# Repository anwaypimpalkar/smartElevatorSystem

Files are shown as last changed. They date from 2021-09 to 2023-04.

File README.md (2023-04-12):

# Smart Elevator Systems using Embedded Machine Learning and Fire Safety Mechanisms

April - June 2021 | Micro Project in SY BTech

### Updates
- ***June 2021:** Awarded "Best Project" out of a pool of 1000+ projects at the 5th IEEE National Level Project Competition.*

- ***January 2022:** Check out the [Arduino Team's Blog Post](https://blog.arduino.cc/2022/01/29/this-contactless-system-combines-embedded-ml-and-sensors-to-improve-elevator-safety/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) covering this project!*

## Introduction

Using an approach of Embedded Machine Learning, we built a multi-tenant architecture to facilitate a contactless elevator system. It consists of two parts – person detection and speech recognition. To create an effective pipeline, we used multiple signal processing techniques to extract necessary features from the input signals. Further, we developed a fire safety system using basic yet functional sensors in two methods – using a microcontroller and using an operational amplifier. These systems are deployed outside and inside an elevator, respectively. Lastly, we built a PCB to house all these components and make a holistically deployable product.

## High-Level Process Flow

First, we would want a person to come and stand in front of the elevator, indicating that he wants to use it. 
Then, the person would speak the floor number he would like to visit, and the elevator system recognizes the floor number which was spoken. The elevator then operates as it should and the doors should open for him. The overall flow of the system is shown in the figure below.

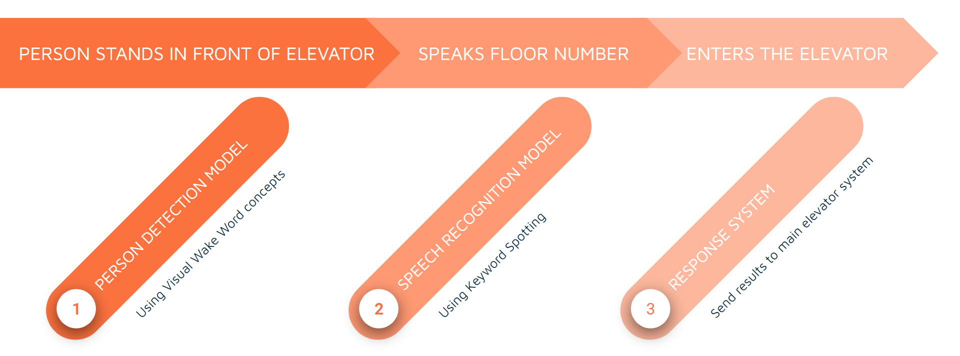
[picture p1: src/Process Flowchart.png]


## System Overview

The project is a three-part system encompassing the following subsystems:

1. Person recognition (VWW Detection) and voice recognition (KWS) to operate the elevator.

2. Fire safety mechanism inside the elevator to drop installed oxygen masks and signal the main elevator interface.

3. Fire safety and detection system outside the elevator on different floors bundled with the features mentioned in point (1).

A generic block diagram of the entire system is shown below.

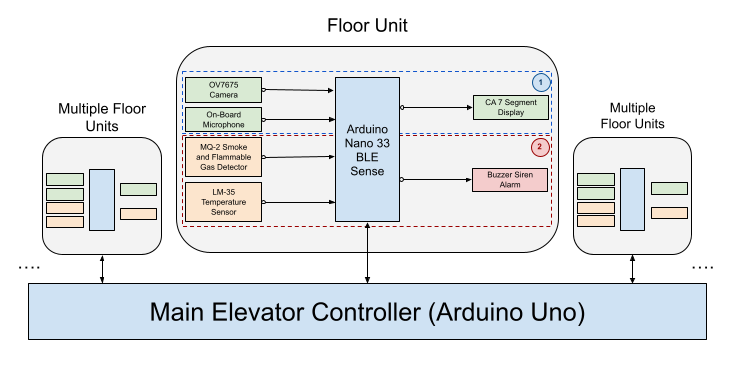
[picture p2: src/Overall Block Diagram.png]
   

## Contactless Operation using KWS and VWW CNN Models

The KWS and VWW models are combined in a multi-tenant architecture. In such a structure, only one of the two models runs inference on the input data at a time. This allows for fast inferences and efficient memory allocation when and wherever required. As our development board of choice - *Arduino Nano 33 BLE Sense*, has limited resources available on board (1MB CPU Flash Memory, 256KB SRAM), the neural network on the system had to be memory and energy efficient compared to a whole scale neural network model. Further post-training quantization methods were implemented to reduce the size of the model (KWS model: 26,720 bytes; VWW model: 3,00,568 bytes; Total size after compilation: 207712 bytes 79% of dynamic memory) and latency of the inferences in real time.

#### Visual Wake Word (VWW) Model for Person Detection

The Visual Wake Word model used for our elevator use case is based on an existing MobileNets model. The core concept behind the architecture is depthwise separable convolution. This is a variant of classical two-dimensional convolutions that works in a much more efficient way, without compromising on accuracy greatly. The model has various steps, as shown in the figure below. Namely, these steps are Initialization, Pre-Processing, Model Inference, and Response.

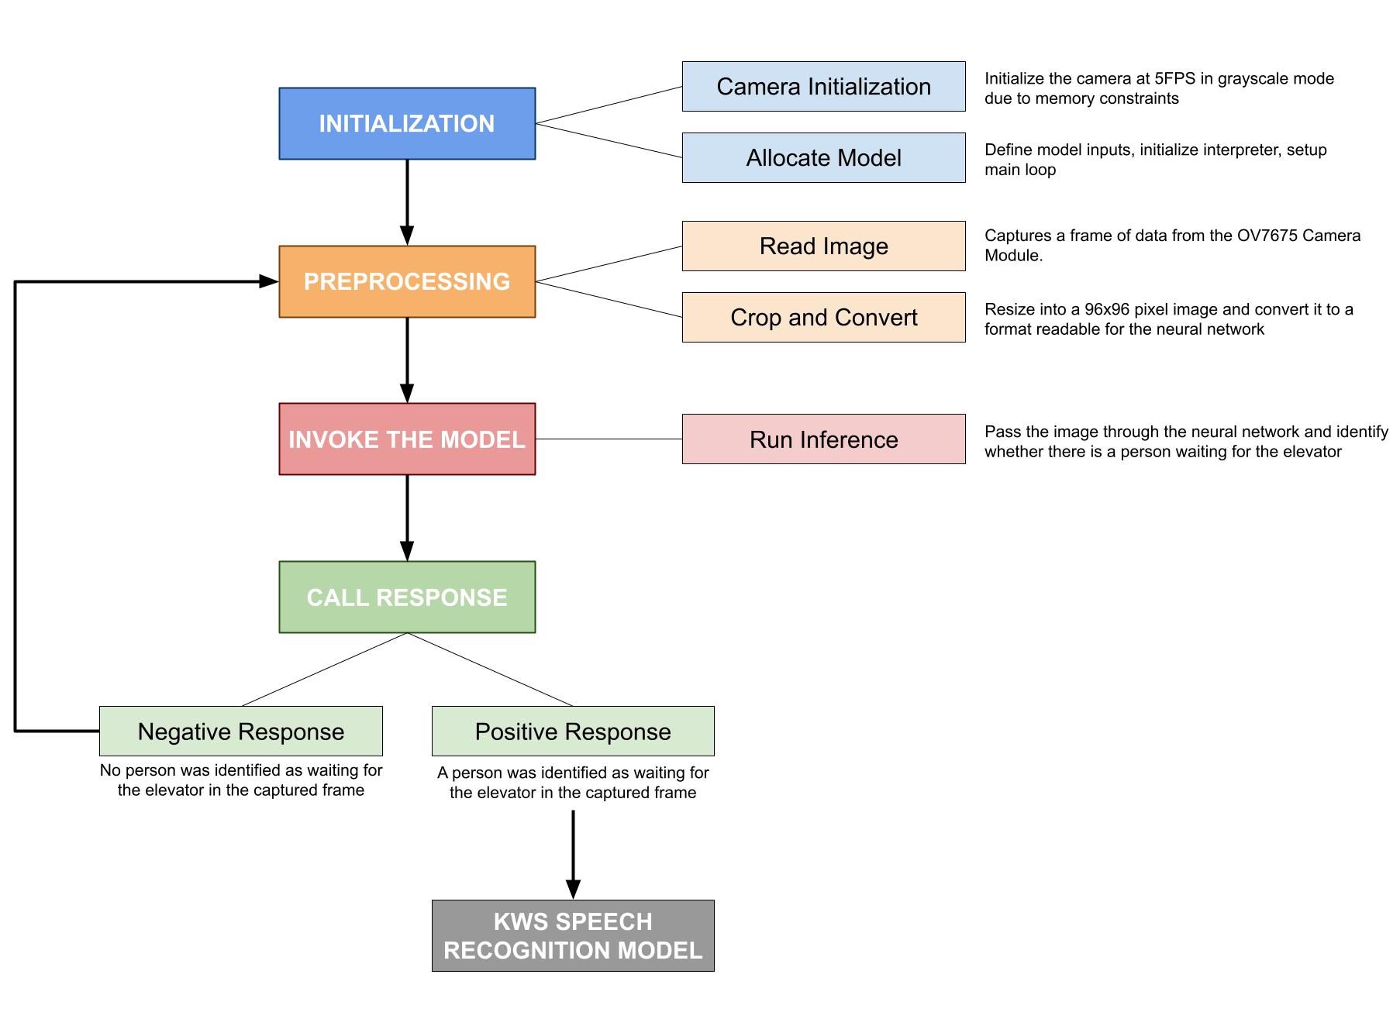
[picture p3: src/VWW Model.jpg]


#### Keyword Spotting (KWS) Model for Speech Recognition

To enable a completely contactless experience for the elevator interface, we implemented a speech recognition approach to choose the floor number that a given user would like to go to. We went on to implement a KWS (Keyword Spotting) model to satisfy this requirement. The chosen keywords were floor numbers in the lower order “One”, “Two”, “Three” and “Four”. Like the VWW model, the KWS model has 4 high level steps in the system as shown in the figure below. Compared to the prior, this model is relatively lightweight and takes lesser time for training and inference.

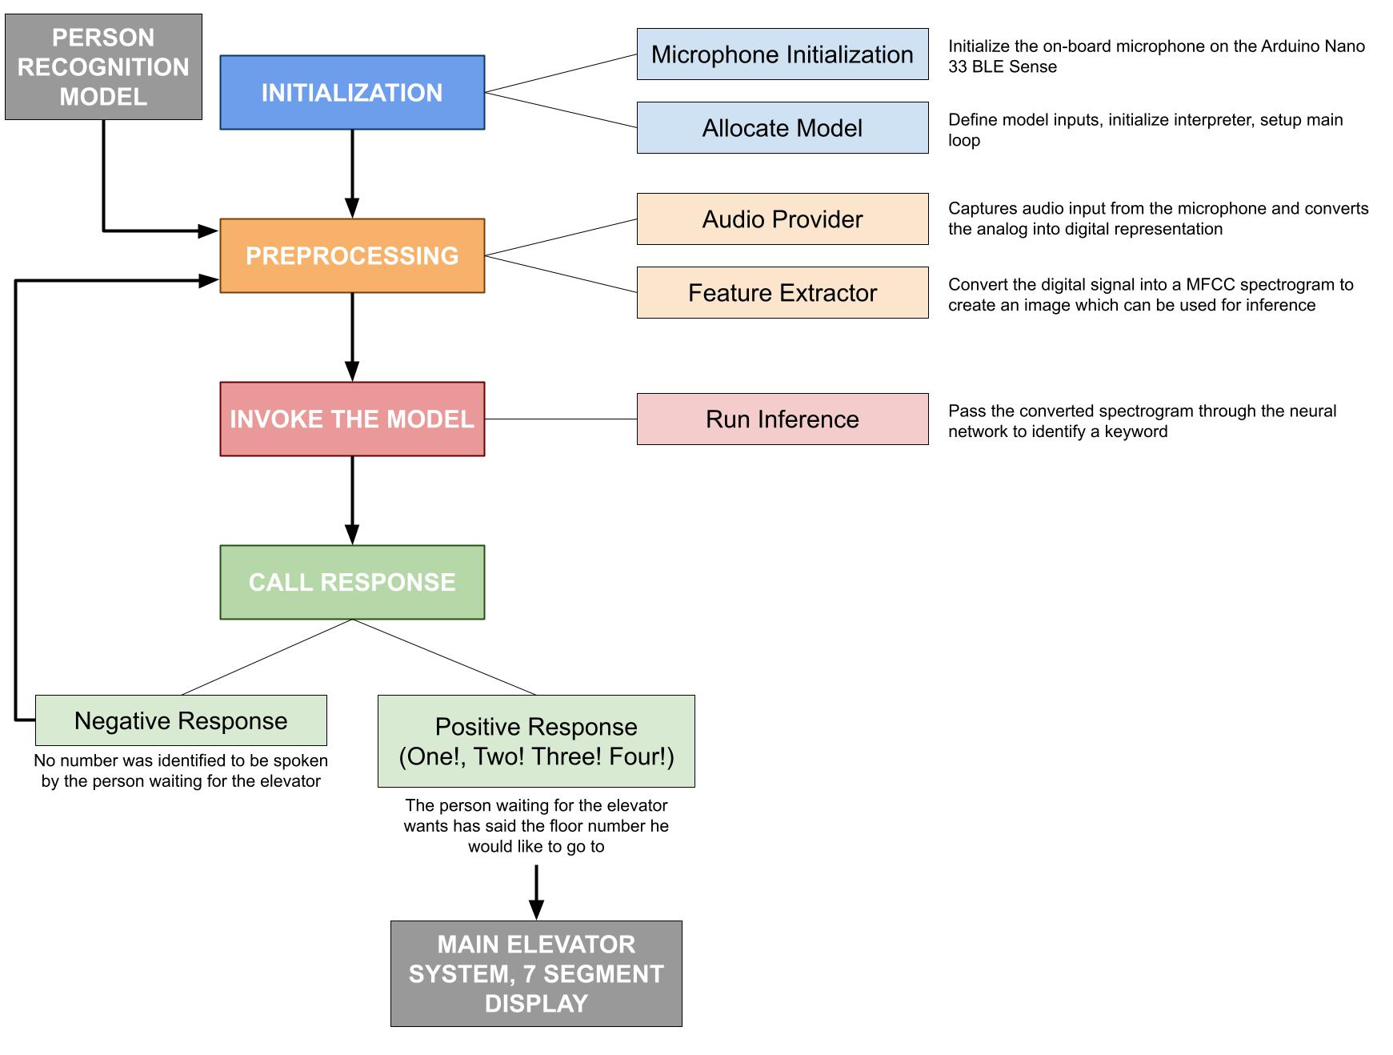
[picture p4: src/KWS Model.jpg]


To make it easier for the CNN to process and classify the audio signals into different categories, we extract the features of the buffer audio sample before passing it into an inference pipeline. The various steps of feature extraction are:

- Fast Fourier Transform (FFT)
- Frequency Domain Spectrograms
- Mel Frequency Cepstral Coefficient Spectrograms

#### Multitenant Architecture for Running KWS and VWW Simultaneously

Due to the memory and power constraints on any embedded microcontroller, running two CNN inference engines simultaneously is a challenge. Our approach to this problem was to implement a multi-tenant architecture for combining the KWS and VWW model. In such a structure, only one of the two models runs inference on the input data at a time. Both models share the TensorArena and use the same memory allocations. This allowed for fast inferences and efficient memory allocation when and wherever required. There is also no requirement for the synchronization of data streams from the camera module and the microphone, both of which are running at different sampling rates.

## Fire Safety System

Elevator shafts may be exposed to smoke and that smoke could reach occupants not just inside the elevator but on other floors as well. In such situations, the elevator is advised to return to the ground floor of the building immediately. The most efficient way to develop a fire safety system which protects the occupants of an elevator is to design a system which works in tandem with it the smoke/flammable gas detectors and temperature sensors directly. To maximize the efficiency of such a system, we developed a pipeline in which the main elevator interface has direct inputs from the smoke detection units. Depending on the levels obtained from the sensors, the elevator interface can further be commanded to execute a specific set of instructions, for example taking the elevator to the lowest floor immediately in the case of a fire.

To implement our approach, we chose to use a MQ-2 Smoke/Flammable Gas Detector and a LM-35 Temperature sensor.

## Implementation and Results

The hardware required for the implementation of the contactless elevator system, i.e., the VWW and KWS models was readily available with us, namely the Arduino Nano 33 BLE Sense and OV7675 Camera Module. They are mounted on a shield for the scope of this experiment. Further into the implementation, we designed our own shield to house the OV7675 and Arduino module along with other peripherals.

Once the shield was properly positioned, we ran inference by standing inside and outside the frame of the camera. As discussed in the System Architecture chapter, each inference returns a probability value between -127 and +127, where higher numbers indicate a higher probability of a human subject being present in the frame.

The camera input of greyscale QCIF images of size 144 x 176 pixels with human subject are shown below.

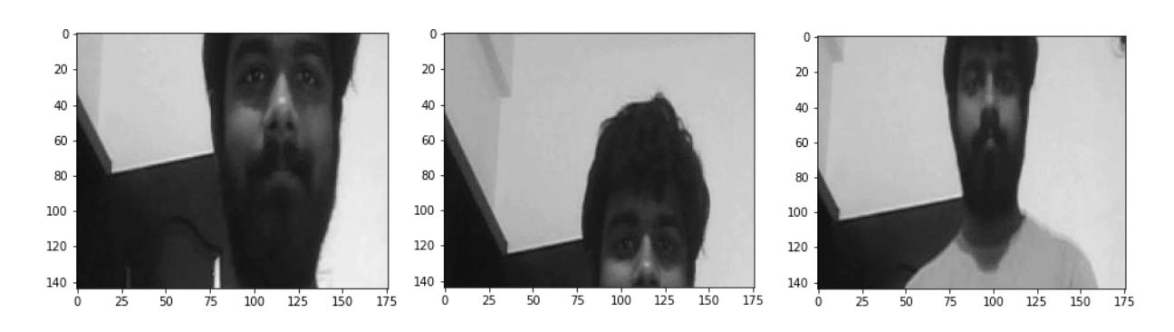
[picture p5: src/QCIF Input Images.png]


Once the inference engine is run, the probability values are generated. These values are printed on the serial monitor of the Arduino IDE. When a person is entering the frame or in motion, the camera is unable to pick up the fast movement due to the low frame rate. At such moments, the model is decisive of whether a person is the frame or not. Hence, while classifying as a human detected in the field of view, we chose to keep a minimum Person score of 25. This threshold value reduces the number of false positives. If a person is detected in the frame, the green RGB light on the Arduino is lit up, whereas when there is no person detected, the red RGB light is lit up.

Once a person has been detected in the frame, the KWS model inference engine is triggered, and the system starts listening for keywords spoken by the user to communicate the floor number which they would like to go to. These numbers are chosen to be “One”, “Two”, “Three”, and “Four”. The incoming audio is sampled at 16 kHz and ran inference on every one second. Whenever the Arduino is listening for a keyword, the yellow light rapidly blinks, and upon positive inference, the blue RGB light is lit up. The different LED states are shown in the image below.

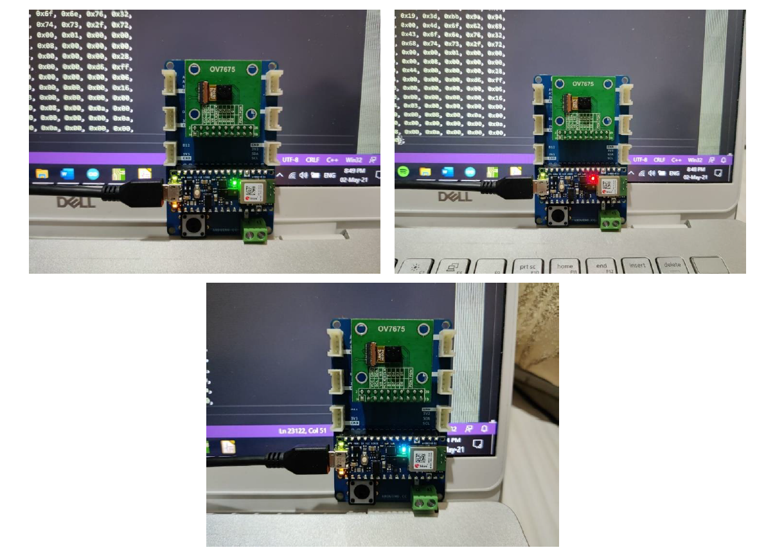
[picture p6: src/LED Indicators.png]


The fire safety system outside the elevator bundled with the deployed unit was simulated on Proteus. The system consisted of the following components:
1. MQ-2 Smoke Detector System
2. LM-35 Temperature Sensor
3. 7 Segment Display using Shift Register
4. Alarm and Connection to Main Elevator Interface

Since the Arduino Nano 33 BLE Sense was not available as a library for simulation, we used the Arduino Nano baseline model for it. The architecture is similar and hence is adequate for the purposes of the project. For the sake of completeness in the project, we chose to go create a pseudo-main elevator interface using an Arduino Uno in the simulation. A 4 x 16 LCD Display was also added for us to keep track of the system status. The figure below shows the circuit schematic for the project on Proteus. The Arduino Nano is interfaced with a LM-35 and MQ-2 sensor, a 7 Segment Display and an alarm system which is triggered when the system is simulating a fire scenario.

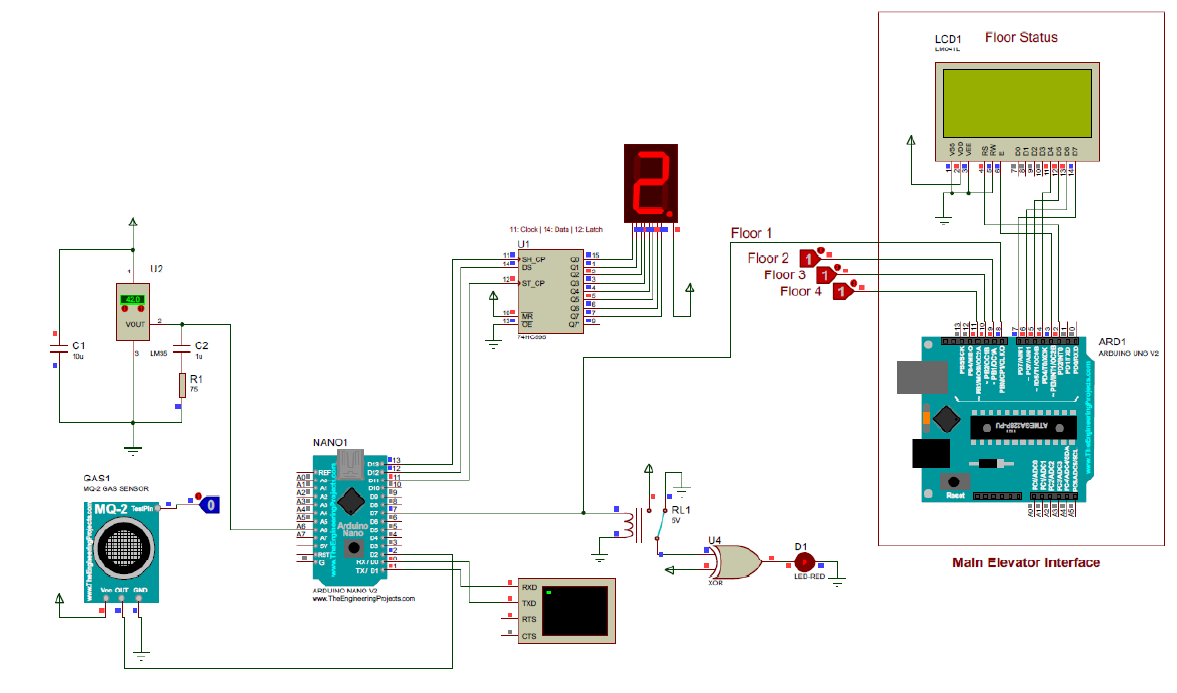
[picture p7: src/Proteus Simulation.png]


#### PCB Design

To house the components of this project, we created a Printed Circuit Board design using KiCAD, an open-source EDA software. Some key specifications of the PCB are:

1. The PCB consists of 4 Copper layers.

2. Front and Back Copper Layers are signal layers.
3. Inner1 Copper layer contains a Power Plane.
4. Inner2 Copper layer contains a Ground Plane.
5. All components used utilize Through Hole Technology (THT) except for 74AHC1G86 Dual Input Single Output EX-OR Gate which uses SMT.

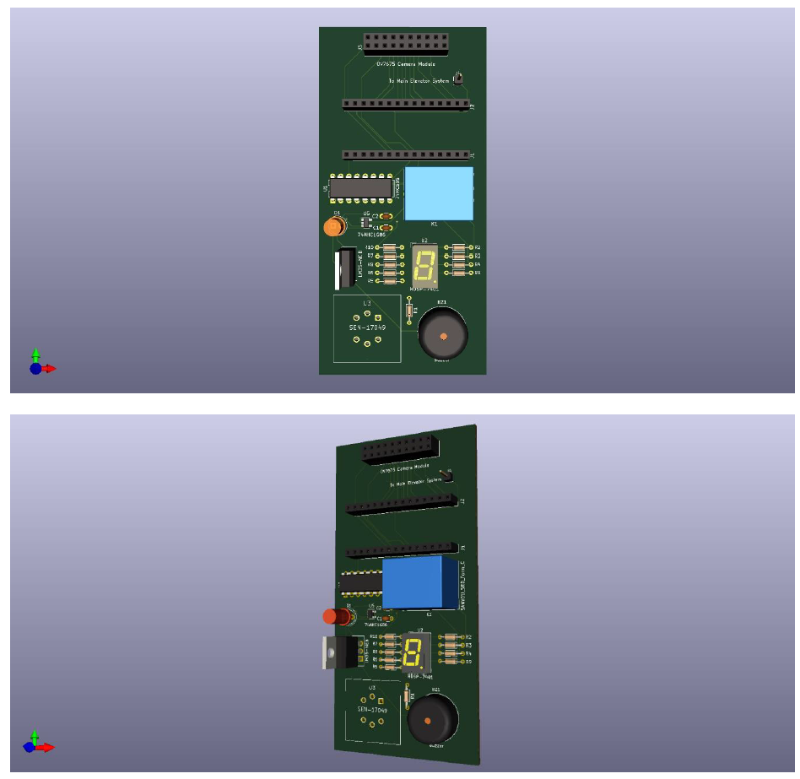
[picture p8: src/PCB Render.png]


## Demonstration

The hardware required was implemented as a proof of concept for the evaluation of the project. An unnarrated [video demonstration](https://youtu.be/mMH1OMFZL_I) has been documented.

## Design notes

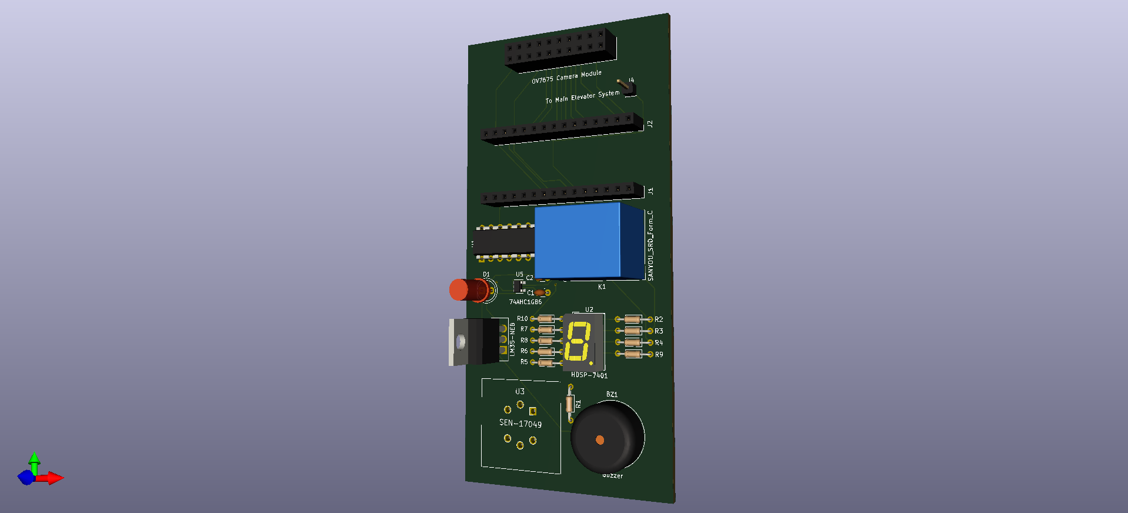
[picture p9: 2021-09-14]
KiCAD PCB Design/PCB Layout/PCB Render - 1.png

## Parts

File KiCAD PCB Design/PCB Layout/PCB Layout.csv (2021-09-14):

Id | Designator | Package | Quantity | Designation | Supplier and ref
1 | K1 | Relay_SPDT_SANYOU_SRD_Series_Form_C | 1 | SANYOU_SRD_Form_C
2 | U3 | SEN17049 | 1 | SEN-17049
3 | U4 | TO-220-3_Vertical | 1 | LM35-NEB
4 | U1 | DIP-16_W7.62mm | 1 | 74HC595
5 | J3 | PinSocket_2x10_P2.54mm_Vertical | 1 | OV7675 Camera Module
6 | J1 | PinSocket_1x15_P2.54mm_Vertical | 1 | L Arduino Mount
7 | J2 | PinSocket_1x15_P2.54mm_Vertical | 1 | R Arduino Mount
8 | U2 | HDSP-7401 | 1 | HDSP-7401
9 | BZ1 | Buzzer_15x7.5RM7.6 | 1 | Buzzer
10 | U5 | SOT-23-5 | 1 | 74AHC1G86
11 | J4 | PinHeader_1x01_P2.54mm_Vertical | 1 | To Main Elevator System
12 | R1 | R_Axial_DIN0204_L3.6mm_D1.6mm_P7.62mm_Horizontal | 1 | 4kΩ
13 | R2,R3,R4,R5,R6,R7,R8,R9 | R_Axial_DIN0204_L3.6mm_D1.6mm_P7.62mm_Horizontal | 8 | 330Ω
14 | C1 | C_Disc_D3.0mm_W1.6mm_P2.50mm | 1 | 10uF
15 | C2 | C_Disc_D3.0mm_W1.6mm_P2.50mm | 1 | 1uF
16 | R10 | R_Axial_DIN0204_L3.6mm_D1.6mm_P7.62mm_Horizontal | 1 | 75Ω
17 | D1 | LED_D5.0mm_FlatTop | 1 | LED

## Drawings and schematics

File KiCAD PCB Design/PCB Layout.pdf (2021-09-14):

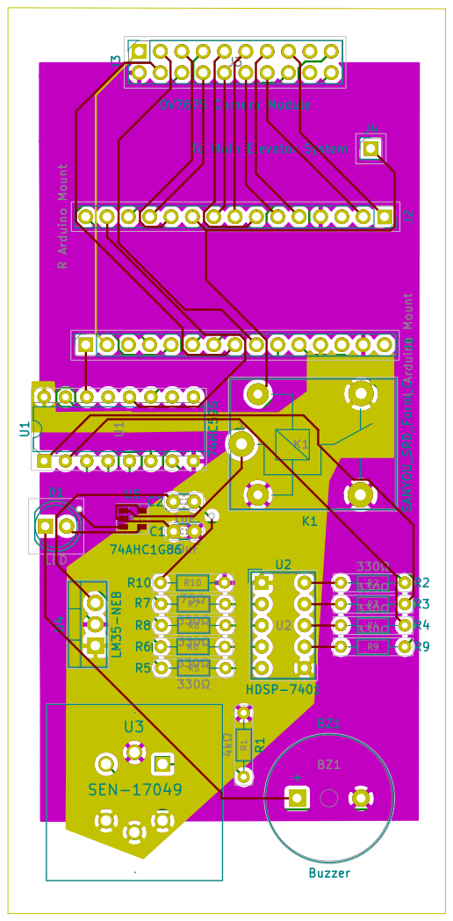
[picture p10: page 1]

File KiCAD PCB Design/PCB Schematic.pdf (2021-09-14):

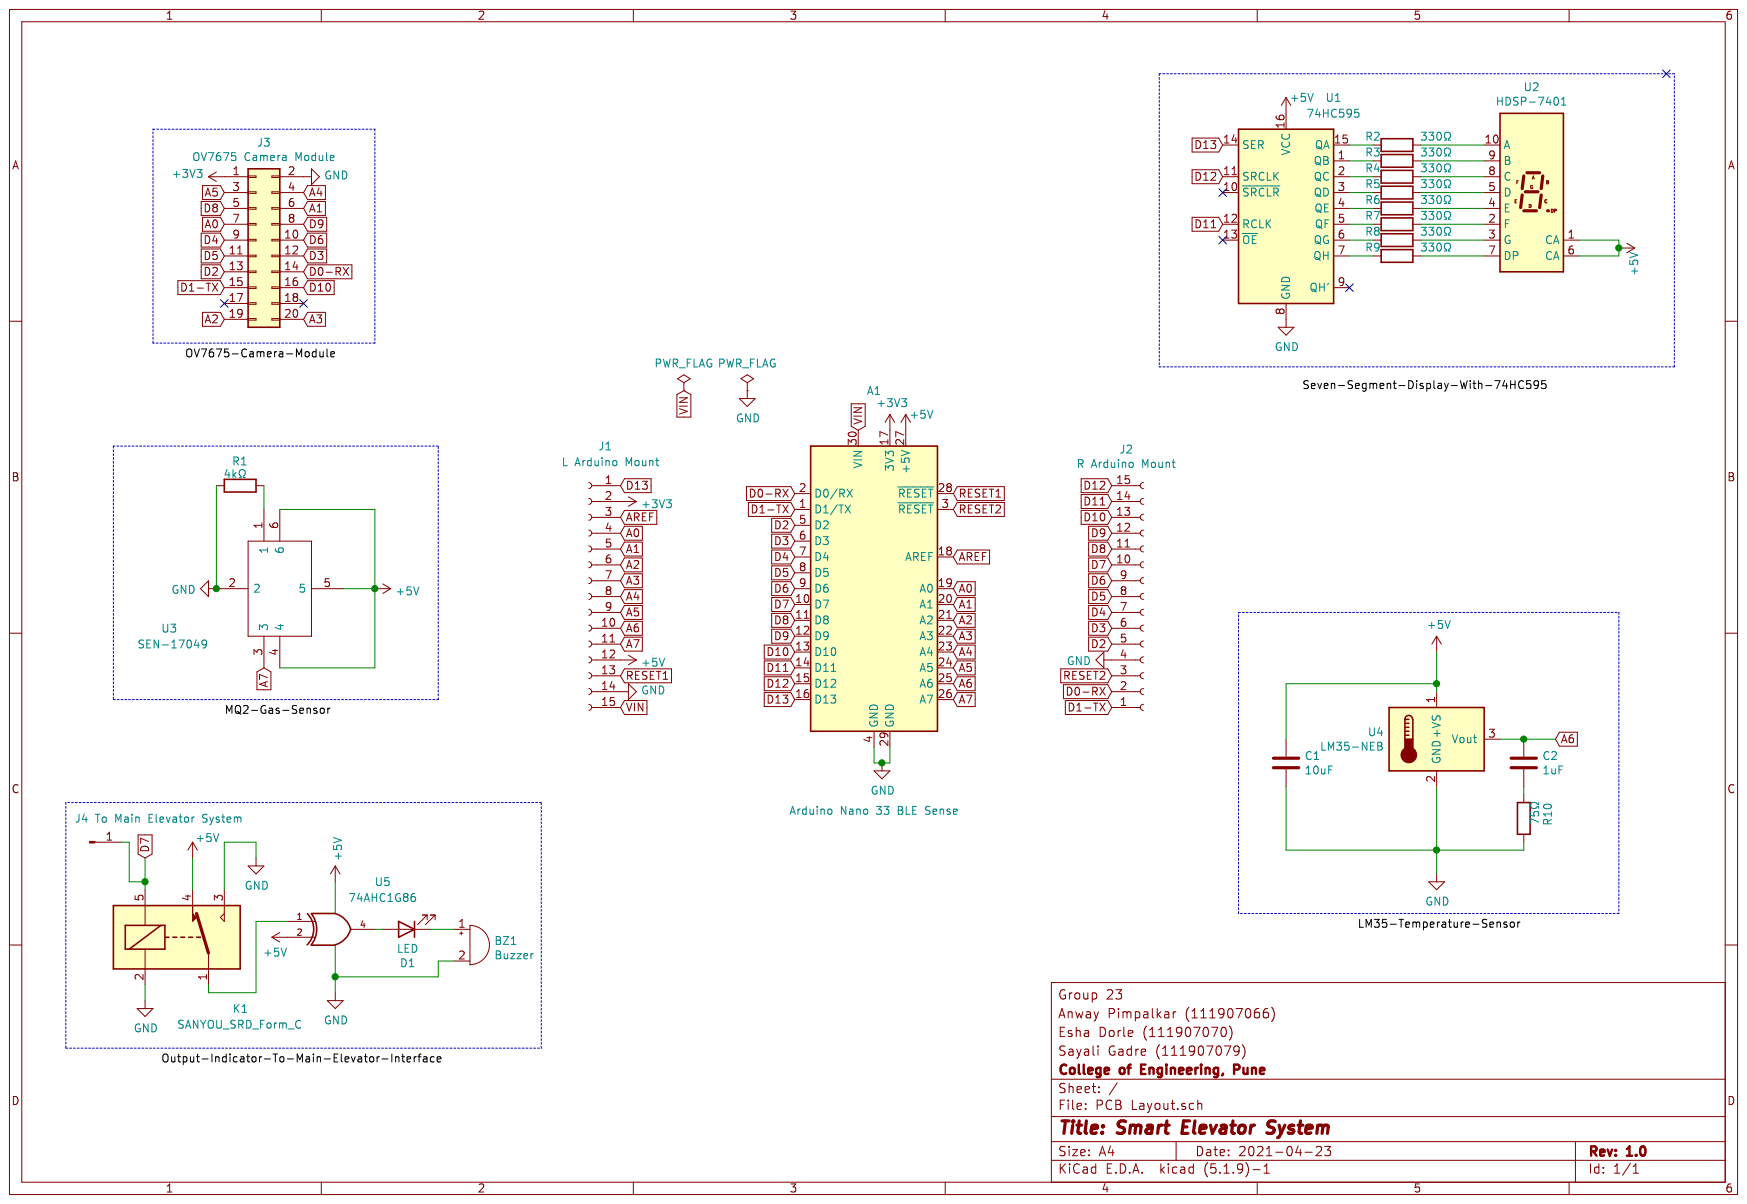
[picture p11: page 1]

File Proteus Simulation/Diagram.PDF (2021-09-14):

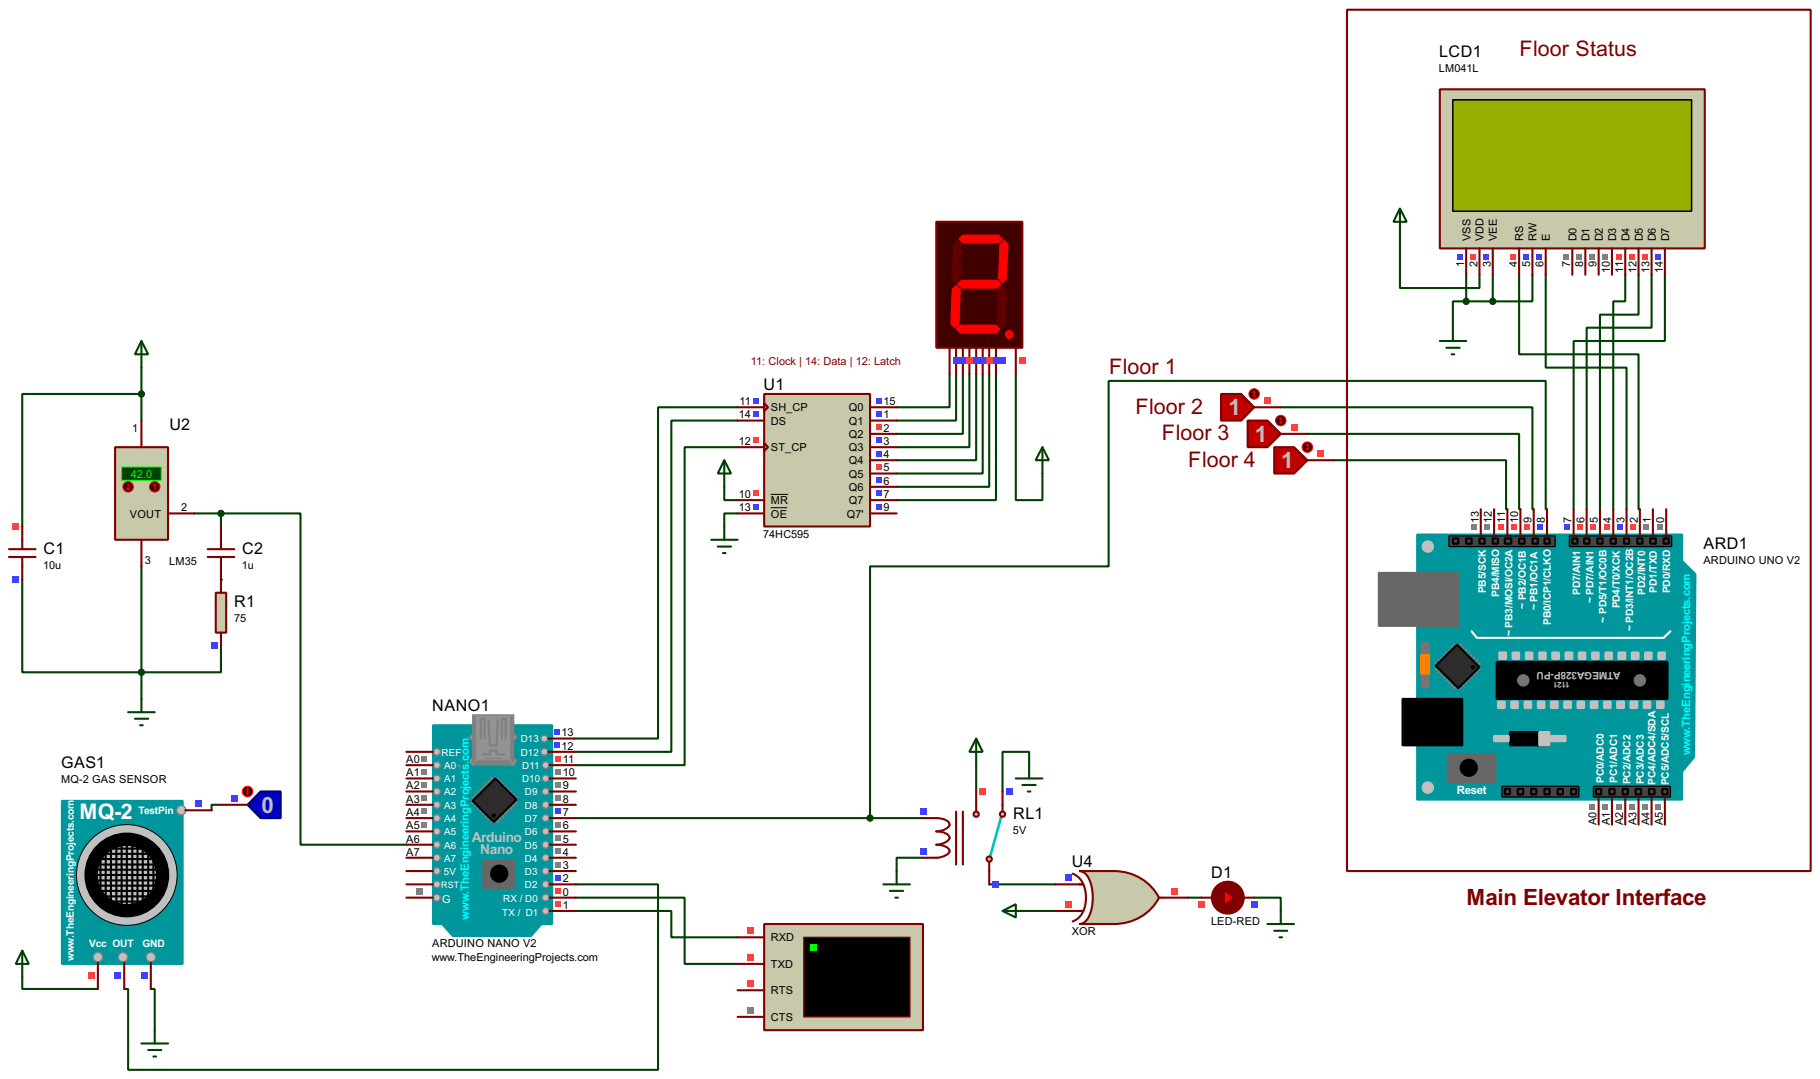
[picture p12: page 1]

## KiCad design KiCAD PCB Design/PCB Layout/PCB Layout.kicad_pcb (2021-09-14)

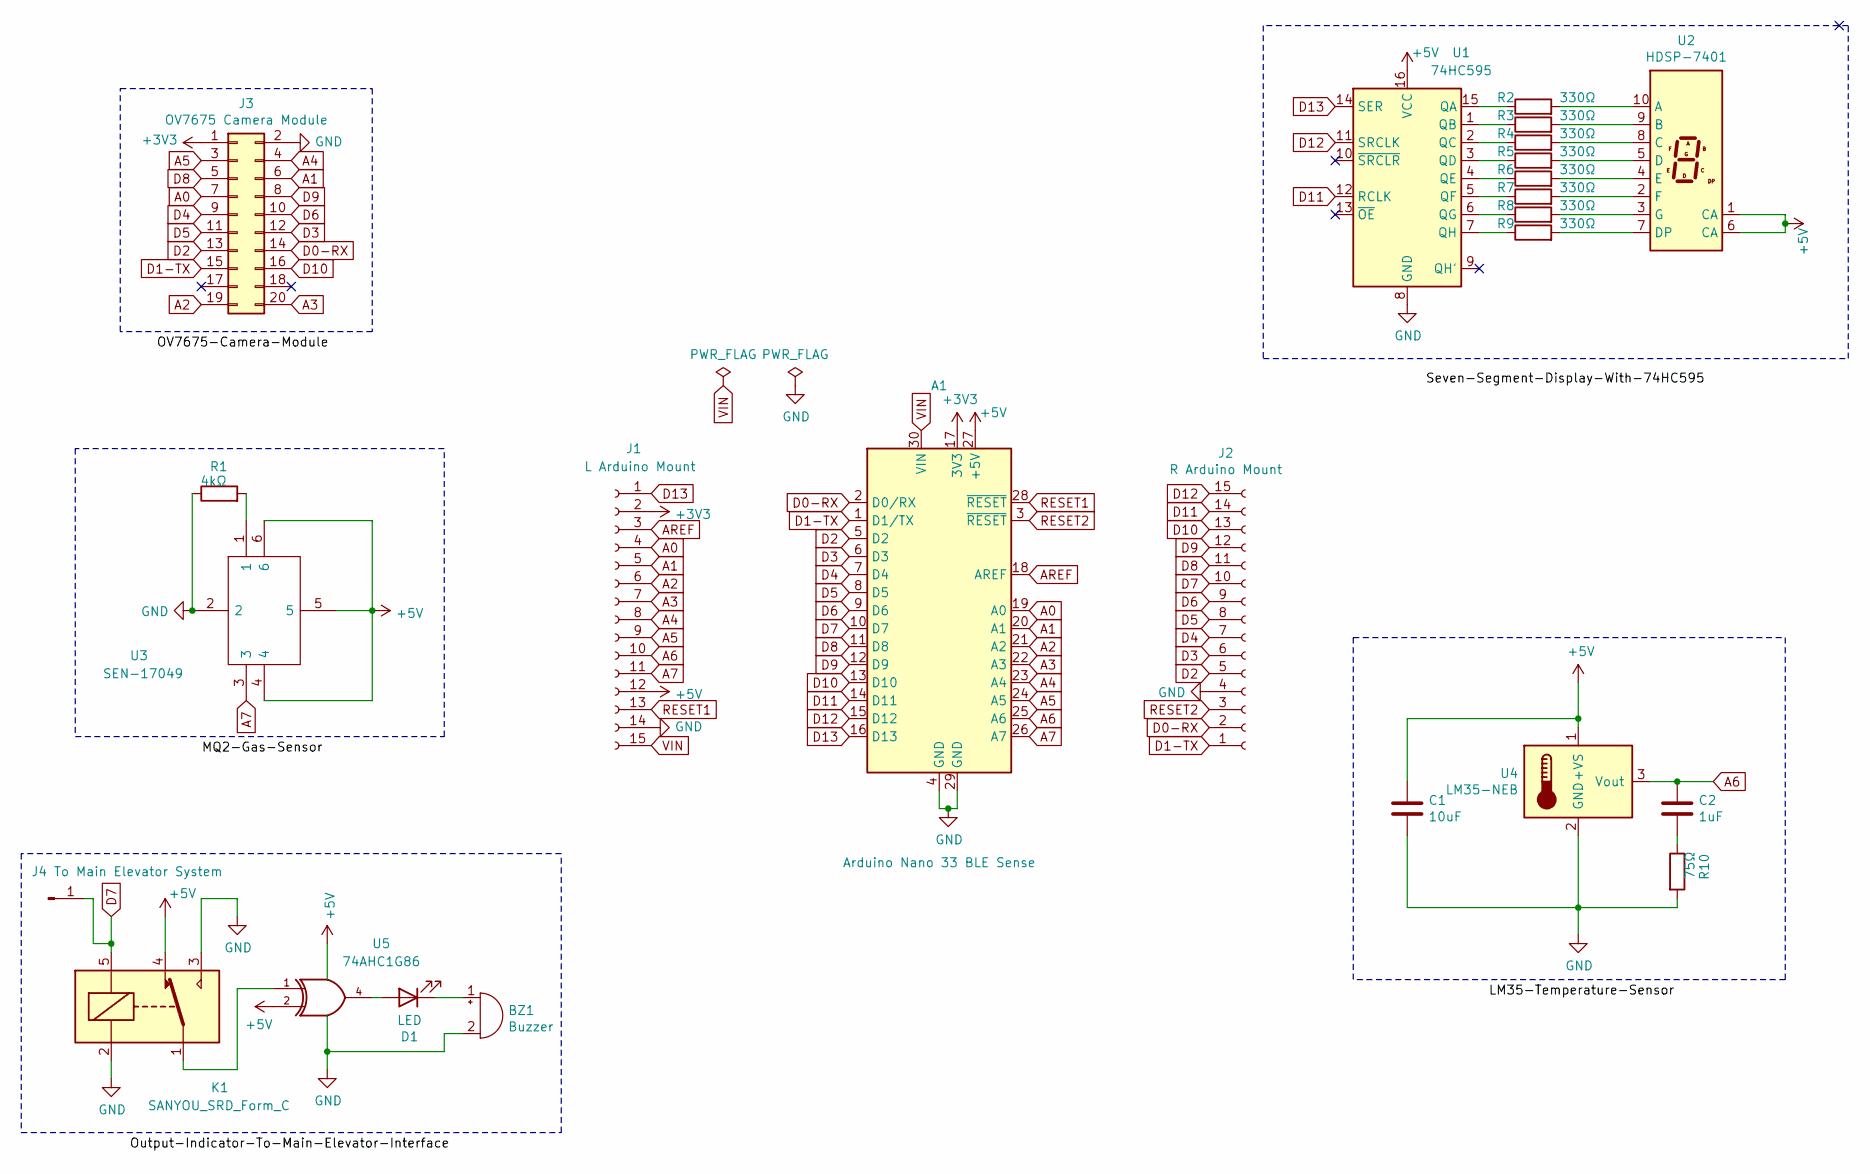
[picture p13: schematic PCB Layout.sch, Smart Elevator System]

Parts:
A1: Arduino Nano 33 BLE Sense; Arduino_Nano
BZ1: Buzzer; Buzzer_15x7.5RM7.6
C1: 10uF; C_Disc_D3.0mm_W1.6mm_P2.50mm
C2: 1uF; C_Disc_D3.0mm_W1.6mm_P2.50mm
D1: LED; LED_D5.0mm_FlatTop
J1: L Arduino Mount; PinSocket_1x15_P2.54mm_Vertical
J2: R Arduino Mount; PinSocket_1x15_P2.54mm_Vertical
J3: OV7675 Camera Module; PinSocket_2x10_P2.54mm_Vertical
J4: To Main Elevator System; PinHeader_1x01_P2.54mm_Vertical
K1: SANYOU_SRD_Form_C; Relay_SPDT_SANYOU_SRD_Series_Form_C
R1: 4kΩ; R_Axial_DIN0204_L3.6mm_D1.6mm_P7.62mm_Horizontal
R2, R3, R4, R5, R6, R7, R8, R9: 330Ω; R_Axial_DIN0204_L3.6mm_D1.6mm_P7.62mm_Horizontal
R10: 75Ω; R_Axial_DIN0204_L3.6mm_D1.6mm_P7.62mm_Horizontal
U1: 74HC595; DIP-16_W7.62mm
U2: HDSP-7401
U3: SEN-17049; SEN17049; Manufacturer_Part_Number SEN-17049
U4: LM35-NEB; TO-220-3_Vertical
U5: 74AHC1G86; SOT-23-5

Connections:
+3V3: A1.17 (3V3), J1.2, J3.1
+5V: A1.27 (+5V), C1.1, J1.12, K1.4, U1.16 (VCC), U2.1 (CA), U2.6 (CA), U3.4, U3.5, U3.6, U4.1 (+VS), U5.2, U5.5 (VCC)
A0: A1.19 (A0), J1.4, J3.7
A1: A1.20 (A1), J1.5, J3.6
A2: A1.21 (A2), J1.6, J3.19
A3: A1.22 (A3), J1.7, J3.20
A4: A1.23 (A4), J1.8, J3.4
A5: A1.24 (A5), J1.9, J3.3
A6: A1.25 (A6), C2.1, J1.10, U4.3 (Vout)
A7: A1.26 (A7), J1.11, U3.3
AREF: A1.18 (AREF), J1.3
D0-RX: A1.2 (D0/RX), J2.2, J3.14
D1-TX: A1.1 (D1/TX), J2.1, J3.15
D2: A1.5 (D2), J2.5, J3.13
D3: A1.6 (D3), J2.6, J3.12
D4: A1.7 (D4), J2.7, J3.9
D5: A1.8 (D5), J2.8, J3.11
D6: A1.9 (D6), J2.9, J3.10
D7: A1.10 (D7), J2.10, J4.1, K1.5
D8: A1.11 (D8), J2.11, J3.5
D9: A1.12 (D9), J2.12, J3.8
D10: A1.13 (D10), J2.13, J3.16
D11: A1.14 (D11), J2.14, U1.12 (RCLK)
D12: A1.15 (D12), J2.15, U1.11 (SRCLK)
D13: A1.16 (D13), J1.1, U1.14 (SER)
GND: A1.4 (GND), A1.29 (GND), BZ1.2 (+), C1.2, J1.14, J2.4, J3.2, K1.2, K1.3, R1.1, R10.2, U1.8 (GND), U3.2, U4.2 (GND), U5.3 (GND)
unnamed: BZ1.1 (-), D1.1 (K)
unnamed: C2.2, R10.1
unnamed: D1.2 (A), U5.4
unnamed: K1.1, U5.1
unnamed: R1.2, U3.1
unnamed: R2.1, U1.15 (QA)
unnamed: R2.2, U2.10 (A)
unnamed: R3.1, U1.1 (QB)
unnamed: R3.2, U2.9 (B)
unnamed: R4.1, U1.2 (QC)
unnamed: R4.2, U2.8 (C)
unnamed: R5.1, U1.3 (QD)
unnamed: R5.2, U2.5 (D)
unnamed: R6.1, U1.4 (QE)
unnamed: R6.2, U2.4 (E)
unnamed: R7.1, U1.5 (QF)
unnamed: R7.2, U2.2 (F)
unnamed: R8.1, U1.6 (QG)
unnamed: R8.2, U2.3 (G)
unnamed: R9.1, U1.7 (QH)
unnamed: R9.2, U2.7 (DP)
RESET1: A1.28 (~RESET), J1.13
RESET2: A1.3 (~RESET), J2.3
VIN: A1.30 (VIN), J1.15

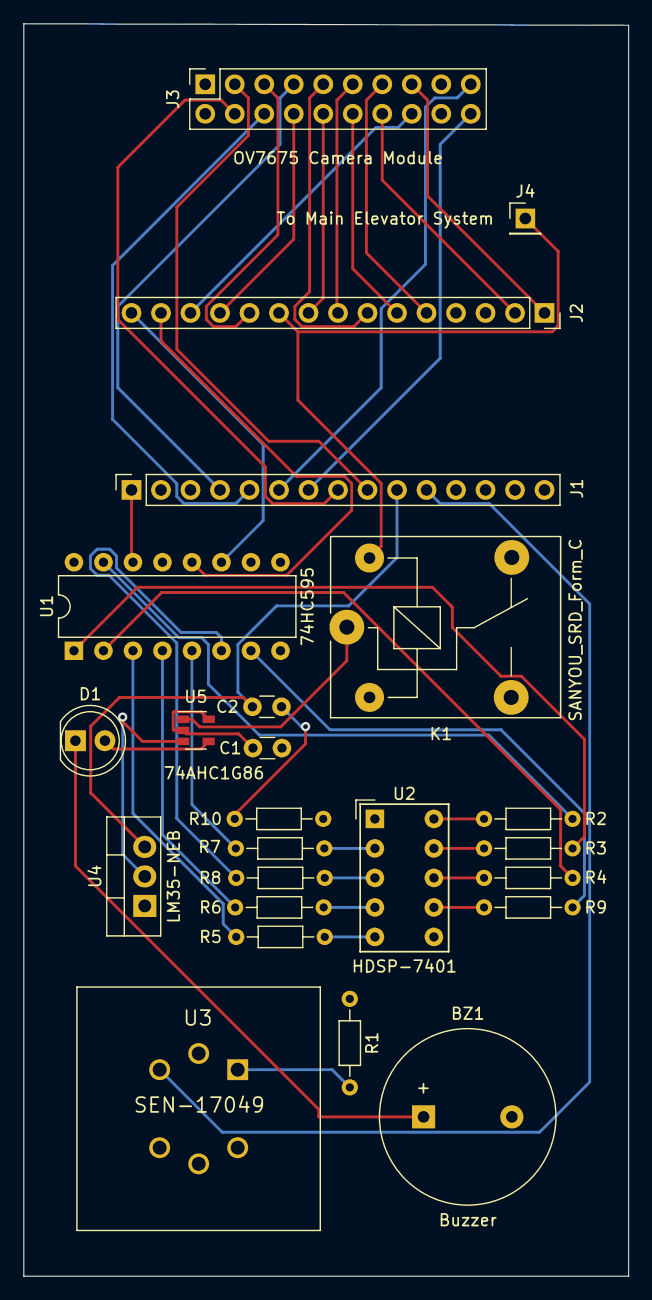
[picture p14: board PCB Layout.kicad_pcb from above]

Board: 4 copper layers, 52.1 x 107.8 mm, 24 parts (0 on the bottom side), 46 nets.

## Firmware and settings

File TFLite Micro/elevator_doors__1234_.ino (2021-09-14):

#include <TensorFlowLite.h>

#include "main_functions.h"
#include "detection_responder.h"
#include "image_provider.h"
#include "model_settings.h"
#include "person_detect_model_data.h"
#include "audio_provider.h"
#include "feature_provider.h"
#include "micro_features_micro_model_settings.h"
#include "micro_features_model.h"
#include "recognize_commands.h"
#include "command_responder.h"
#include "tensorflow/lite/micro/micro_error_reporter.h"
#include "tensorflow/lite/micro/micro_interpreter.h"
#include "tensorflow/lite/micro/micro_mutable_op_resolver.h"
#include "tensorflow/lite/schema/schema_generated.h"
#include "tensorflow/lite/version.h"
#include "Arduino.h"

// Declaration of global variables
namespace
{
tflite::ErrorReporter *error_reporter = nullptr;

const tflite::Model *vww_model = nullptr;
tflite::MicroInterpreter *vww_interpreter = nullptr;
TfLiteTensor *vww_input = nullptr;
TfLiteTensor *vww_output = nullptr;

const tflite::Model *kws_model = nullptr;
tflite::MicroInterpreter *kws_interpreter = nullptr;
TfLiteTensor *kws_input = nullptr;
TfLiteTensor *kws_output = nullptr;
FeatureProvider *feature_provider = nullptr;
RecognizeCommands *recognizer = nullptr;
int32_t previous_time = 0;
int8_t feature_buffer[kFeatureElementCount];
int8_t *model_input_buffer = nullptr;

// An area of memory to use for input, output, and intermediate arrays
constexpr int kTensorArenaSize = 136 * 1024;
static uint8_t tensor_arena[kTensorArenaSize];
}

void setup()
{
  // Set up error handler
  static tflite::MicroErrorReporter micro_error_reporter;
  error_reporter = &micro_error_reporter;

  //create the allocator that will be shared between the VWW and KWS models
  tflite::MicroAllocator *allocator =
    tflite::MicroAllocator::Create(tensor_arena, kTensorArenaSize,
                                   error_reporter);

  // Map the model into a usable data structure from the binary weights
  vww_model = tflite::GetModel(g_person_detect_model_data);
  if (vww_model->version() != TFLITE_SCHEMA_VERSION)
  {
    TF_LITE_REPORT_ERROR(error_reporter,
                         "Model provided is schema version %d not equal "
                         "to supported version %d.",
                         vww_model->version(), TFLITE_SCHEMA_VERSION);
    return;
  }

  // Pull in only the operation implementations we need
  static tflite::MicroMutableOpResolver<6> micro_op_resolver;
  micro_op_resolver.AddAveragePool2D();
  micro_op_resolver.AddConv2D();
  micro_op_resolver.AddDepthwiseConv2D();
  micro_op_resolver.AddReshape();
  micro_op_resolver.AddSoftmax();
  micro_op_resolver.AddFullyConnected();

  //Build an interpreter to run the VWW model
  static tflite::MicroInterpreter vww_static_interpreter(
    vww_model, micro_op_resolver, allocator, error_reporter);
  vww_interpreter = &vww_static_interpreter;

  //Allocate the VWW model from tensor_arena
  TfLiteStatus allocate_status = vww_interpreter->AllocateTensors();
  if (allocate_status != kTfLiteOk)
  {
    TF_LITE_REPORT_ERROR(error_reporter, "AllocateTensors() failed");
    return;
  }

  vww_input = vww_interpreter->input(0);
  vww_output = vww_interpreter->output(0);

  //Initialize the KWS model
  kws_model = tflite::GetModel(g_model);
  if (kws_model->version() != TFLITE_SCHEMA_VERSION)
  {
    TF_LITE_REPORT_ERROR(error_reporter,
                         "Model provided is schema version %d not equal "
                         "to supported version %d.",
                         kws_model->version(), TFLITE_SCHEMA_VERSION);
    return;
  }

  //Build an interpreter to run the KWS model. The allocator is reused
  static tflite::MicroInterpreter kws_static_interpreter(
    kws_model, micro_op_resolver, allocator, error_reporter);
  kws_interpreter = &kws_static_interpreter;

  //Allocate the KWS model from tensor_arena. Some head space is saved
  allocate_status = kws_interpreter->AllocateTensors();
  if (allocate_status != kTfLiteOk)
  {
    TF_LITE_REPORT_ERROR(error_reporter, "AllocateTensors() failed");
    return;
  }

  kws_input = kws_interpreter->input(0);
  kws_output = kws_interpreter->output(0);
  model_input_buffer = kws_input->data.int8;

  // Prepare to access the audio spectrograms from a microphone that will provide the inputs to the neural network
  static FeatureProvider static_feature_provider(kFeatureElementCount,
      feature_buffer);
  feature_provider = &static_feature_provider;

  static RecognizeCommands static_recognizer(error_reporter);
  recognizer = &static_recognizer;

  previous_time = 0;
}

void loop()
{

  // Get image from camera
  if (kTfLiteOk != GetImage(error_reporter, kNumCols, kNumRows, kNumChannels,
                            vww_input->data.int8))
  {
    TF_LITE_REPORT_ERROR(error_reporter, "Image capture failed.");
  }

  // Run the model on this input
  if (kTfLiteOk != vww_interpreter->Invoke())
  {
    TF_LITE_REPORT_ERROR(error_reporter, "Invoke failed.");
  }

  // Process the inference results.
  int8_t person_score = vww_output->data.uint8[kPersonIndex];
  int8_t no_person_score = vww_output->data.uint8[kNotAPersonIndex];
  RespondToDetection(error_reporter, person_score, no_person_score);

  //
  bool ifPerson = person_score > 20;

  if (ifPerson)
  {
    unsigned long start_time = millis();
    while (millis() - start_time < 5000)
    {
      // Fetch the spectrogram for the current time.
      const int32_t current_time = LatestAudioTimestamp();
      int how_many_new_slices = 0;
      TfLiteStatus feature_status = feature_provider->PopulateFeatureData(
                                      error_reporter, previous_time, current_time, &how_many_new_slices);
      if (feature_status != kTfLiteOk)
      {
        TF_LITE_REPORT_ERROR(error_reporter, "Feature generation failed");
        return;
      }
      previous_time = current_time;
      // If no new audio samples have been received since last time, don't bother running the network model.
      if (how_many_new_slices == 0)
      {
        return;
      }

      // Copy feature buffer to input tensor
      for (int i = 0; i < kFeatureElementCount; i++)
      {
        model_input_buffer[i] = feature_buffer[i];
      }

      // Run the model on the spectrogram input and make sure it succeeds.
      TfLiteStatus invoke_status = kws_interpreter->Invoke();
      if (invoke_status != kTfLiteOk)
      {
        TF_LITE_REPORT_ERROR(error_reporter, "Invoke failed");
        return;
      }

      const char *found_command = nullptr;
      uint8_t score = 0;
      bool is_new_command = false;
      TfLiteStatus process_status = recognizer->ProcessLatestResults(
                                      kws_output, current_time, &found_command, &score, &is_new_command);
      if (process_status != kTfLiteOk)
      {
        TF_LITE_REPORT_ERROR(error_reporter, "RecognizeCommands::ProcessLatestResults() failed");
        return;
      }
      // Respond to command, show digit on 7 segment display
      RespondToCommand(error_reporter, current_time, found_command, score,
                       is_new_command);
    }
  }
}

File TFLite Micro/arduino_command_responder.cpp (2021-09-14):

#if defined(ARDUINO) && !defined(ARDUINO_ARDUINO_NANO33BLE)
#define ARDUINO_EXCLUDE_CODE
#endif // defined(ARDUINO) && !defined(ARDUINO_ARDUINO_NANO33BLE)

#ifndef ARDUINO_EXCLUDE_CODE

#include "command_responder.h"

#include "Arduino.h"

// Toggles the built-in LED every inference, and lights a colored LED depending
// on which word was detected.
void RespondToCommand(tflite::ErrorReporter *error_reporter,
                      int32_t current_time, const char *found_command,
                      uint8_t score, bool is_new_command)
{
    static bool is_initialized = false;
    if (!is_initialized)
    {
        pinMode(LED_BUILTIN, OUTPUT);
        // Pins for the built-in RGB LEDs on the Arduino Nano 33 BLE Sense
        pinMode(LEDR, OUTPUT);
        pinMode(LEDG, OUTPUT);
        pinMode(LEDB, OUTPUT);
        // Ensure the LED is off by default.
        // Note: The RGB LEDs on the Arduino Nano 33 BLE Sense are on when the pin is LOW, off when HIGH.
        digitalWrite(LEDR, HIGH);
        digitalWrite(LEDG, HIGH);
        digitalWrite(LEDB, HIGH);
        is_initialized = true;
    }
    static int32_t last_command_time = 0;
    static int count = 0;
    static int certainty = 220;

    if (is_new_command)
    {
        TF_LITE_REPORT_ERROR(error_reporter, "Heard %s (%d) @%dms", found_command,
                             score, current_time);
        // If we hear a command, light up the appropriate LED
        if (found_command[0] == 'o')
        {
            last_command_time = current_time;
            digitalWrite(LEDB, LOW);
            Serial.println("One!");
        }

        if (found_command[0] == 't' and found_command[1] == 'w')
        {
            last_command_time = current_time;
            digitalWrite(LEDB, LOW);
            Serial.println("Two!");
        }
        if (found_command[0] == 't' and found_command[1] == 'h')
        {
            last_command_time = current_time;
            digitalWrite(LEDB, LOW);
            Serial.println("Three!");
        }
        if (found_command[0] == 'f')
        {
            last_command_time = current_time;
            digitalWrite(LEDB, LOW);
            Serial.println("Four!");
        }
        if (found_command[0] == 'u')
        {
            last_command_time = current_time;
            Serial.print("Unknown!");
        }
    }

    // If last_command_time is non-zero but was >3 seconds ago, zero it
    // and switch off the LED.
    if (last_command_time != 0)
    {
        if (last_command_time < (current_time - 3000))
        {
            last_command_time = 0;
            digitalWrite(LED_BUILTIN, LOW);
            digitalWrite(LEDR, HIGH);
            digitalWrite(LEDG, HIGH);
            digitalWrite(LEDB, HIGH);
        }
        // If it is non-zero but <3 seconds ago, do nothing.
        return;
    }

    // Otherwise, toggle the LED every time an inference is performed.
    ++count;
    if (count & 1)
    {
        digitalWrite(LED_BUILTIN, HIGH);
    }
    else
    {
        digitalWrite(LED_BUILTIN, LOW);
    }
}

#endif // ARDUINO_EXCLUDE_CODE
